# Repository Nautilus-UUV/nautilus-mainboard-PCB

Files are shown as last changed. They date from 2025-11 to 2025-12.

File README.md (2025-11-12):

# Nautilus Mainboard PCB
## Overview
This PCB houses an [STM32H7B0RBT6](https://www.st.com/resource/en/datasheet/stm32h7b0ab.pdf) together with a [CM4](https://pip-assets.raspberrypi.com/categories/634-raspberry-pi-compute-module-4/documents/RP-008168-DS-1-cm4-datasheet.pdf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). The STM32 is primarily used for communication over CanOpen with all the other PCBs while the CM4 is intended to run higher level calculations and then being shut off again. The CM4 is connected to an SSD. The CM4 and STM are connected over Uart (RX, TX) closely for communication and there is an integrated option for the STM to power off and on the CM4. (Currently the CM4's RUN_PG is connected to the STM32's pin number 10.) The STM has a crystal while the CM4 currently does not have one since it was not requested.

Additionally the mainboard provides two IMUs ([BMI088](https://www.bosch-sensortec.com/media/boschsensortec/downloads/datasheets/bst-bmi088-ds001.pdf)) that can be accessed over I^2C by the STM32. Those components house accelerometers and gyroscopes for orientation and movement detection and listen to the following addresses:
- Accelerometer: 0x18, 0x19
- Gyroscope: 0x68, 0x69

The Power supply is primarily provided by the UUV's battery lines (5V, 3.3V and GND) but the board also accepts USB-C 2.0 for both data and power inputs (only powering the CM4 and nothing else) or the 3.3V Power supply over the STM programmer pins. (only powers the STM32) The power logic is achieved using three [TPS2121RUXT](https://www.ti.com/lit/ds/symlink/tps2120.pdf?ts=1761678178328) (one for 5V, one for 3.3V and one for the GPIO reference of both microcontrollers.)

> [!CAUTION]
> The Power supply logic can be bypassed completely by soldering on 0 Ohm resistors on the designated spots for both 5V and 3.3V, but this still needs to be worked on.

### WIP

Differential pairs have been routed and matched in length but the trace widths still need to be recalculated and adjusted.

The whole board works on 2 layers with an additional ground layer in mind (until now 1 free layer)

If someone wants to write a better README, feel free to do so, I'd appreciate it.

This PCB has not yet been reviewed or tested.

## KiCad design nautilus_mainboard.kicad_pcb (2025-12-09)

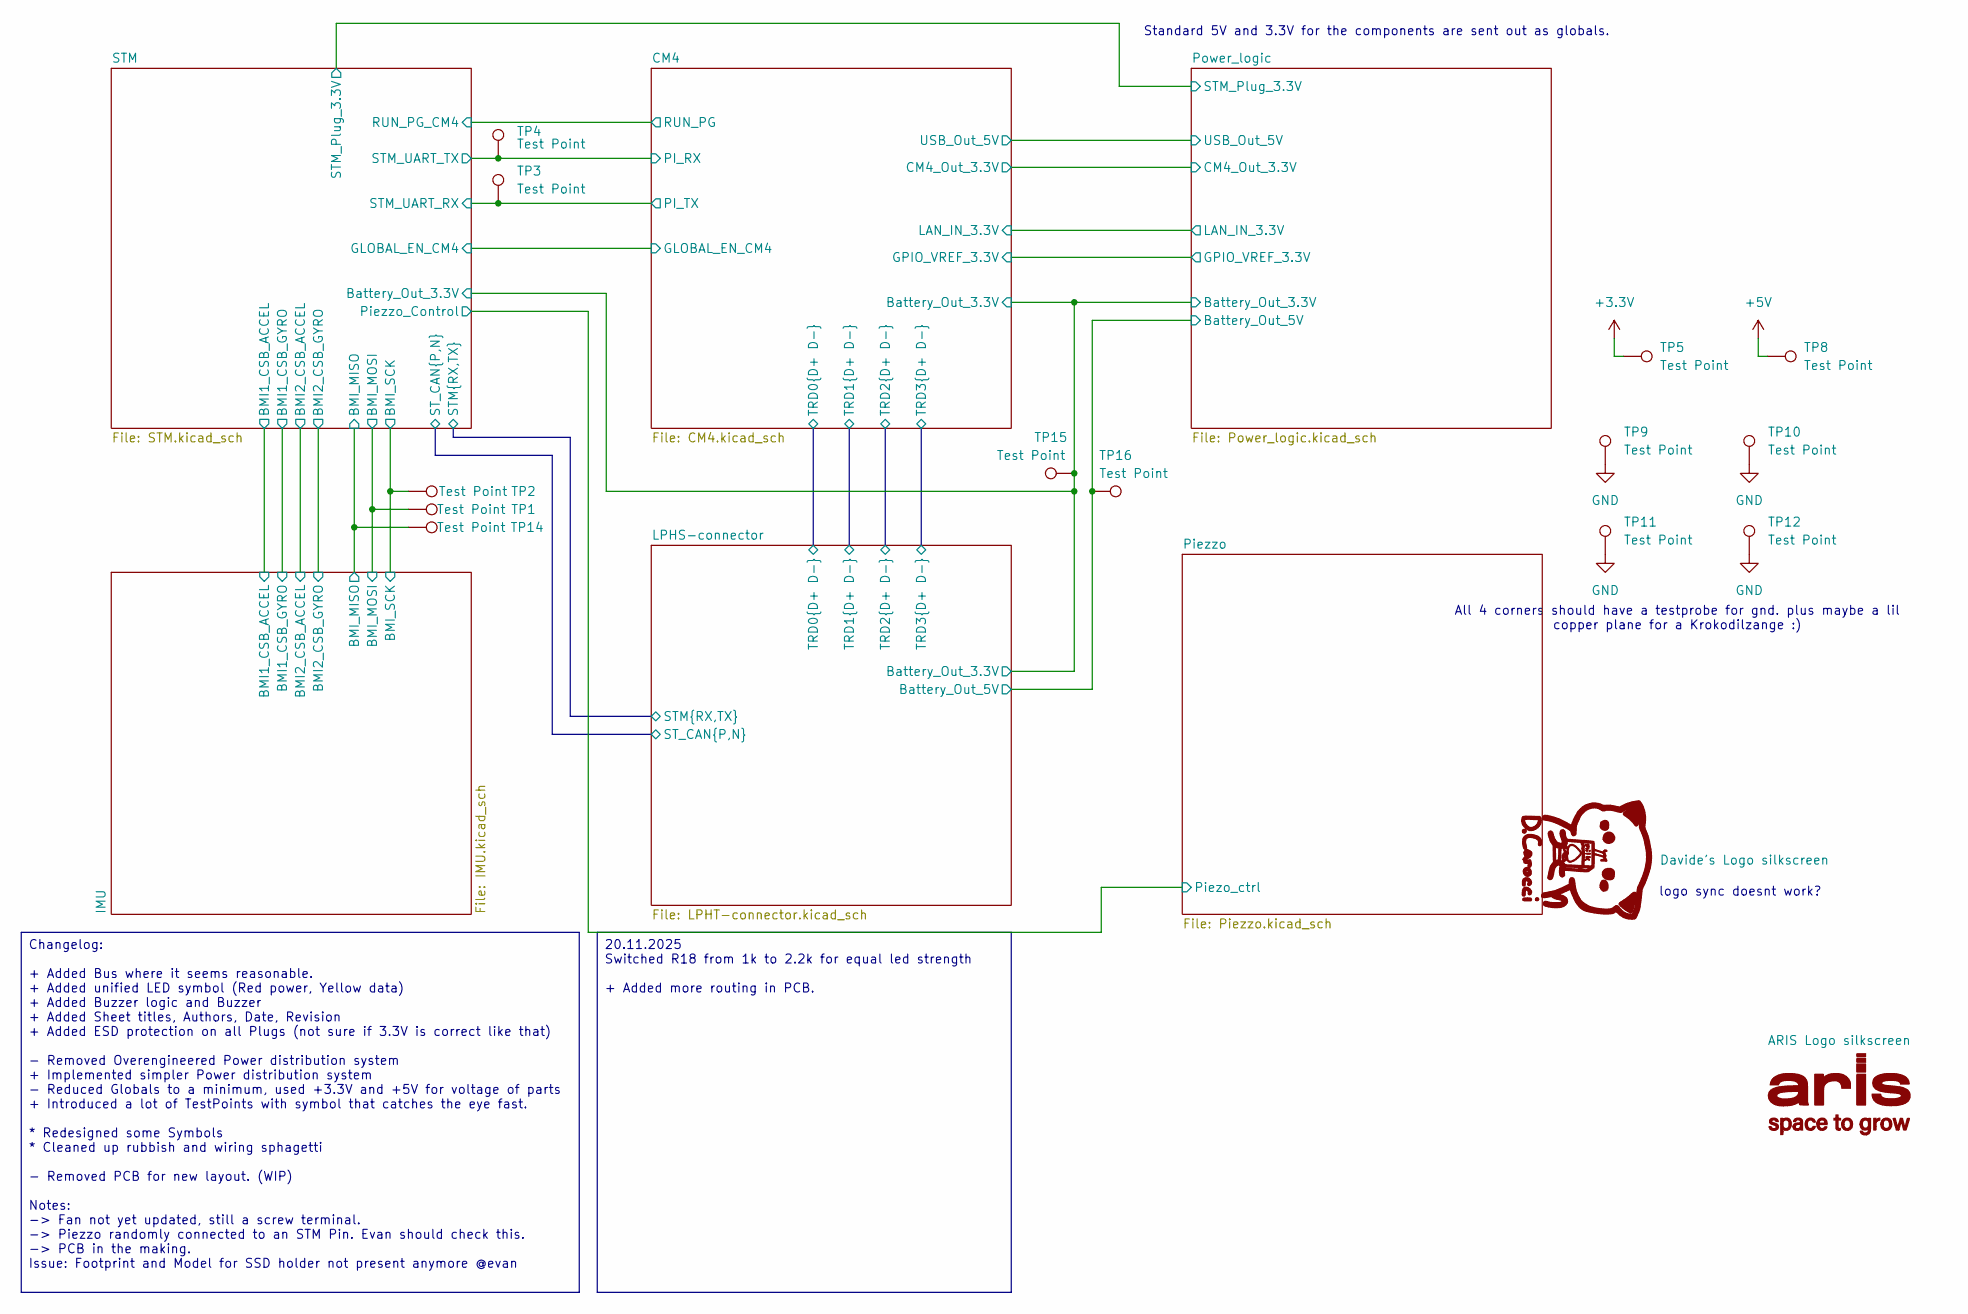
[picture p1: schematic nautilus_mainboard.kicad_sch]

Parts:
TP1, TP2, TP3, TP4, TP5, TP8, TP9, TP10, TP11, TP12, TP14, TP15, TP16: Test Point; TestPoint_Pad_D1.5mm

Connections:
+3.3V: TP5.1; also elsewhere on the board
+5V: TP8.1; also elsewhere on the board
/CM4/Battery_Out_3.3V: TP15.1; also elsewhere on the board
/IMU/BMI_MISO: TP14.1; also elsewhere on the board
/IMU/BMI_MOSI: TP1.1; also elsewhere on the board
/IMU/BMI_SCK: TP2.1; also elsewhere on the board
/LPHS-connector/Battery_Out_5V: TP16.1; also elsewhere on the board
/STM/PinoutSTM/USART2_RX: TP3.1; also elsewhere on the board
/STM/PinoutSTM/USART2_TX: TP4.1; also elsewhere on the board
GND: TP9.1, TP10.1, TP11.1, TP12.1; also elsewhere on the board

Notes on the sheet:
Standard 5V and 3.3V for the components are sent out as globals.
All 4 corners should have a testprobe for gnd. plus maybe a lil copper plane for a Krokodilzange :)
logo sync doesnt work?
20.11.2025 Switched R18 from 1k to 2.2k for equal led strength + Added more routing in PCB.
Changelog: + Added Bus where it seems reasonable. + Added unified LED symbol (Red power, Yellow data) + Added Buzzer logic and Buzzer + Added Sheet titles, Authors, Date, Revision + Added ESD protection on all Plugs (not sure if 3.3V is correct like that) - Removed Overengineered Power distribution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

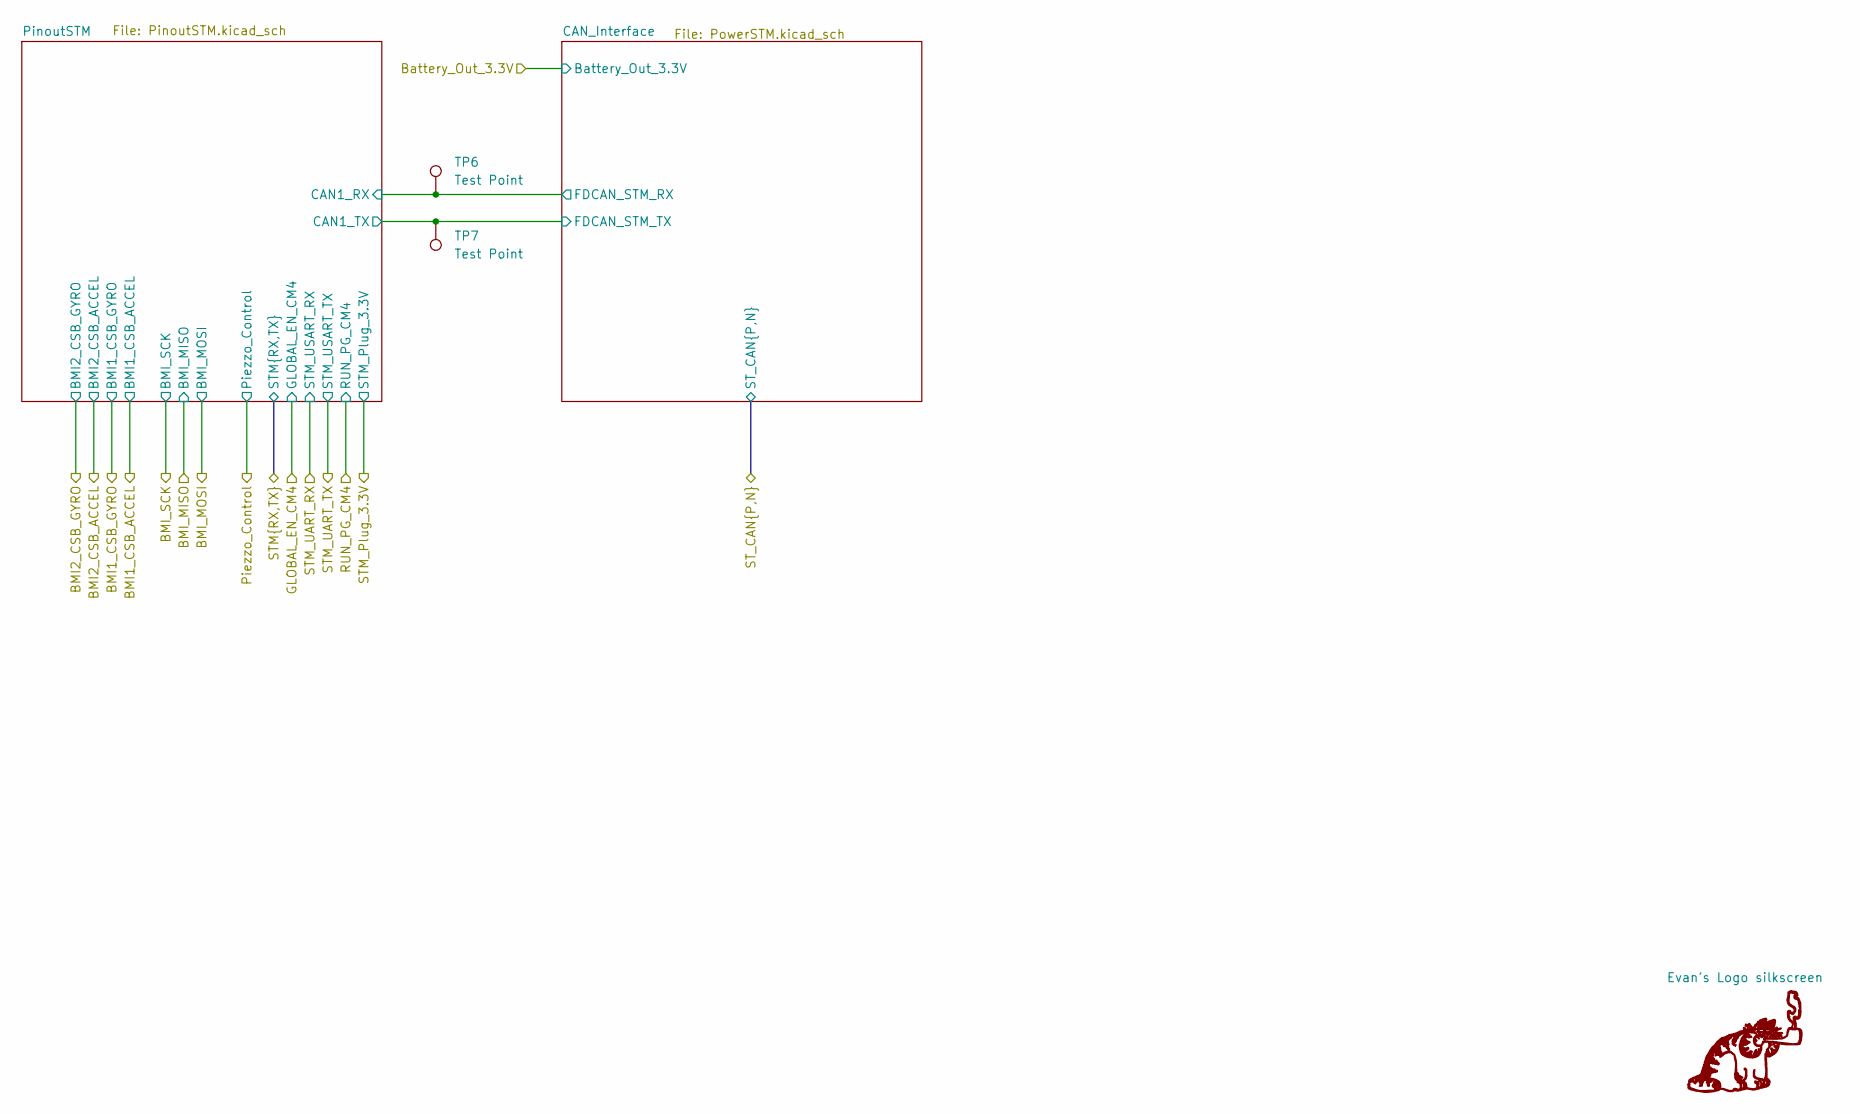
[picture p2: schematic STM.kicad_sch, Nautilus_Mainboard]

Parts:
TP6, TP7: Test Point; TestPoint_Pad_D1.5mm

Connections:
/STM/PinoutSTM/CAN1_RX: TP6.1; also elsewhere on the board
/STM/PinoutSTM/CAN1_TX: TP7.1; also elsewhere on the board

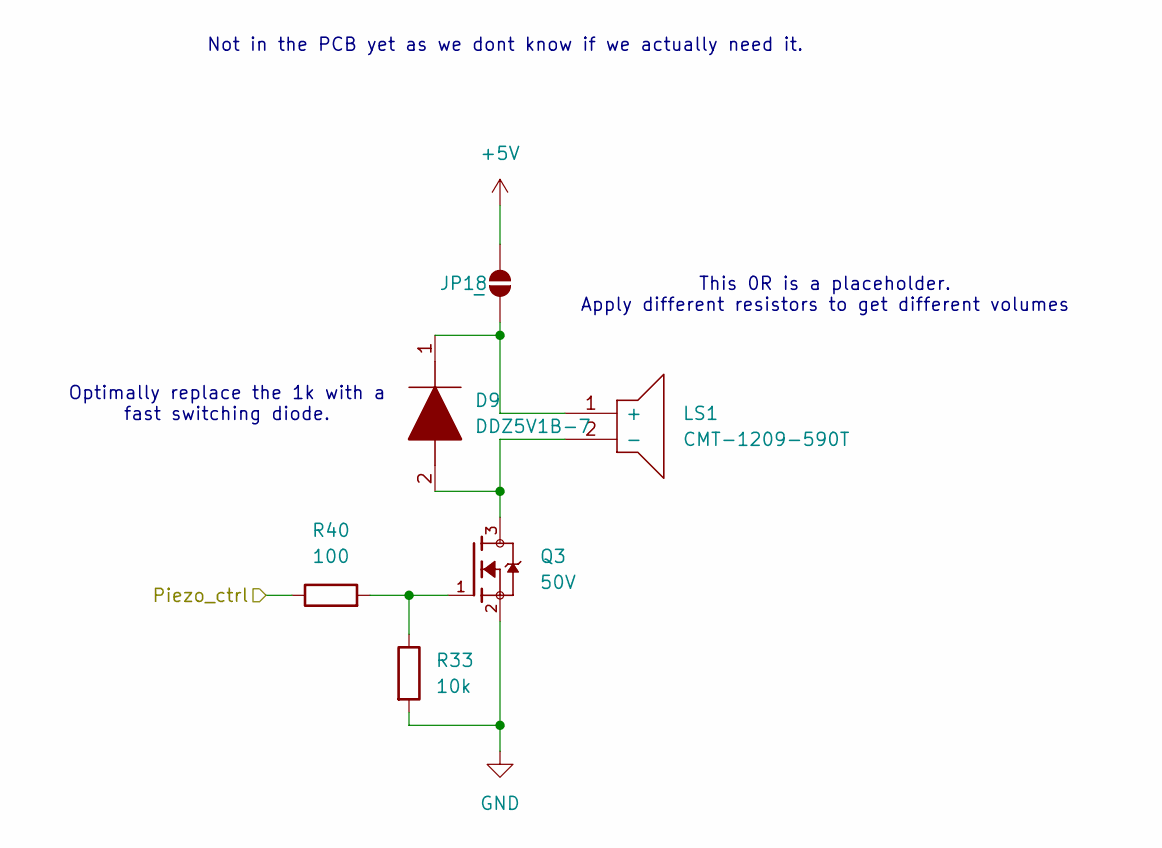
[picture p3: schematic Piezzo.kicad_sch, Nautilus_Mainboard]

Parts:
D9: DDZ5V1B-7; SOD3716X145N; Mouser Part Number 621-DDZ5V1B-7
JP18: -; SolderJumper-2_P1.3mm_Open_RoundedPad1.0x1.5mm
LS1: Piezo Buzzers & Audio Indicators 12mmx9mm deep Ma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; CMT1209590T; Mouser Part Number 179-CMT-1209-590T
Q3: 50V; onsemi_Mosfet_BSS138; PARTREV 30 Jan 2018
R33: 10k; R_0603_1608Metric; Tolerance 1 %; MPN 560112116005; LCSC CXXXXX
R40: 100; R_0402_1005Metric; Tolerance 1%; MPN ERJ-2RKF1000X; LCSC C413063

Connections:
+5V: JP18.2 (B); also elsewhere on the board
/Piezzo/Piezo_ctrl: R40.1; also elsewhere on the board
GND: Q3.2, R33.2; also elsewhere on the board
unnamed: D9.1, JP18.1 (A), LS1.1 (+)
unnamed: D9.2, LS1.2 (-), Q3.3
unnamed: Q3.1, R33.1, R40.2

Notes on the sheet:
Optimally replace the 1k with a fast switching diode.
This 0R is a placeholder. Apply different resistors to get different volumes
Not in the PCB yet as we dont know if we actually need it.

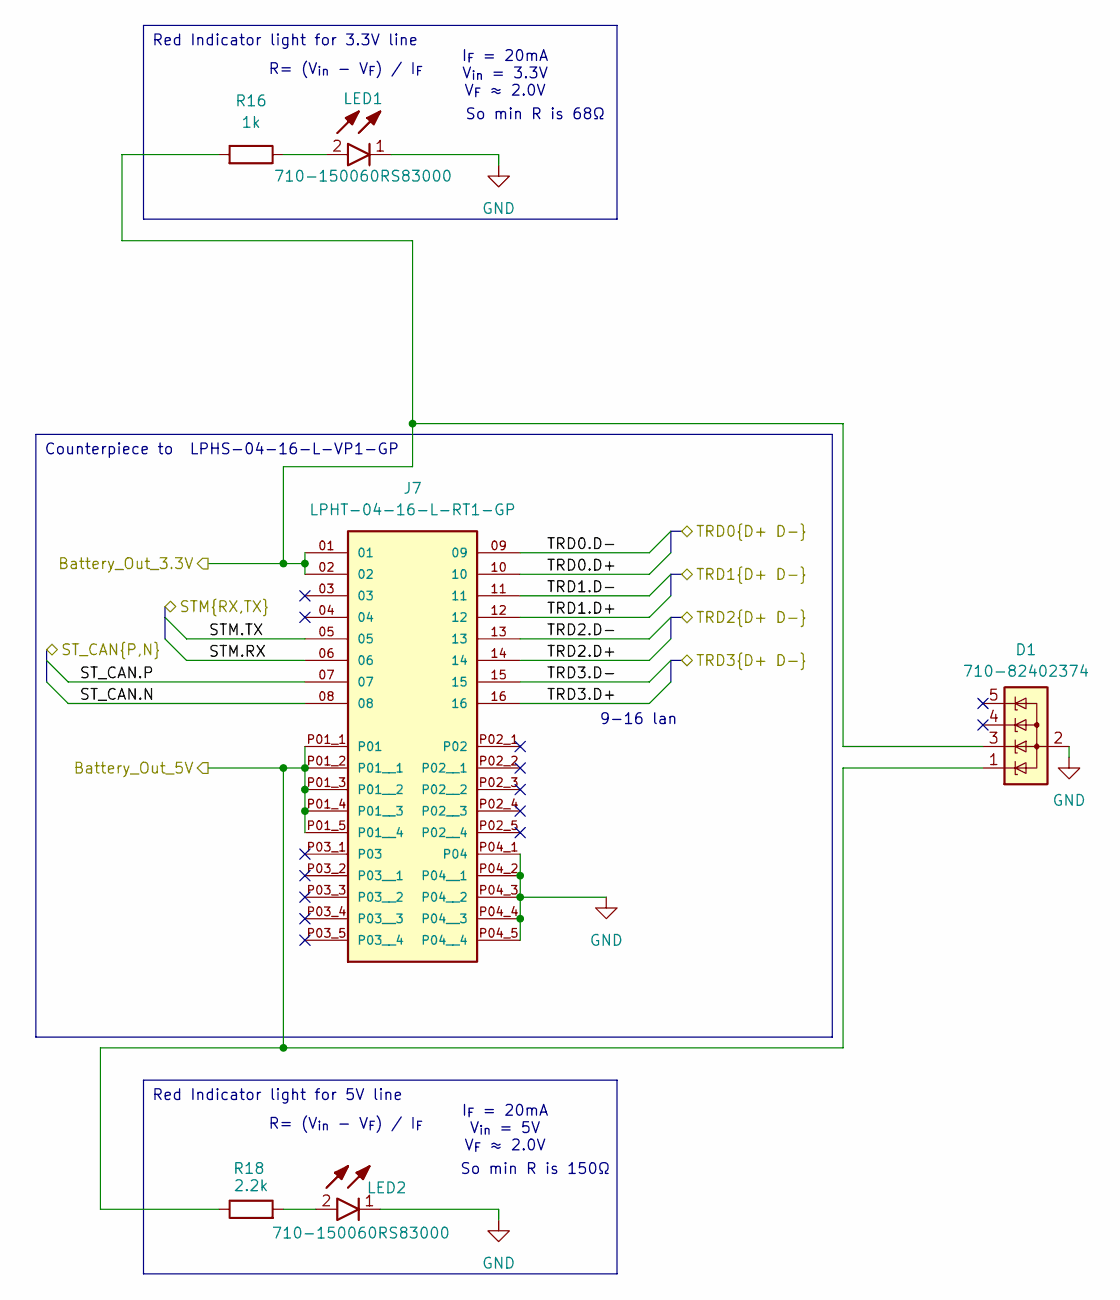
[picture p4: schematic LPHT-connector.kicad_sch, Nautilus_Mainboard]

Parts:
D1: 710-82402374; SOT-23-5; MPN 710-82402374
J7: LPHT-04-16-L-RT1-GP; SAMTEC_LPHT-04-16-X-RT1-GP; PARTREV C; LCSC CXXXXX
LED1, LED2: 710-150060RS83000; Wuerth_LED_150060RS83000; Manufacturer_Part_Number 150060RS83000
R16: 1k; R_0603_1608Metric; Tolerance 1 %; MPN 560112116014; LCSC CXXXXX
R18: 2.2k; R_0603_1608Metric; Tolerance 1 %; MPN 560112116098; LCSC CXXXXX

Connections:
/CM4/Battery_Out_3.3V: D1.3 (K), J7.01, J7.02, R16.2; also elsewhere on the board
/CM4/TRD0.D+: J7.10; also elsewhere on the board
/CM4/TRD0.D-: J7.09; also elsewhere on the board
/CM4/TRD1.D+: J7.12; also elsewhere on the board
/CM4/TRD1.D-: J7.11; also elsewhere on the board
/CM4/TRD2.D+: J7.14; also elsewhere on the board
/CM4/TRD2.D-: J7.13; also elsewhere on the board
/CM4/TRD3.D+: J7.16; also elsewhere on the board
/CM4/TRD3.D-: J7.15; also elsewhere on the board
/LPHS-connector/Battery_Out_5V: D1.1 (K), J7.P01_1 (P01), J7.P01_2 (P01__1), J7.P01_3 (P01__2), J7.P01_4 (P01__3), J7.P01_5 (P01__4), R18.1; also elsewhere on the board
/LPHS-connector/STM.RX: J7.06; also elsewhere on the board
/LPHS-connector/STM.TX: J7.05; also elsewhere on the board
/LPHS-connector/ST_CAN.N: J7.08; also elsewhere on the board
/LPHS-connector/ST_CAN.P: J7.07; also elsewhere on the board
GND: D1.2 (A), J7.P04_1 (P04), J7.P04_2 (P04__1), J7.P04_3 (P04__2), J7.P04_4 (P04__3), J7.P04_5 (P04__4), LED1.1 (K), LED2.1 (K); also elsewhere on the board
unnamed: LED1.2 (A), R16.1
unnamed: LED2.2 (A), R18.2

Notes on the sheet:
9-16 lan
I_{F} = 20mA V_{in} = 5V V_{F} ≈ 2.0V
R= (V_{in} - V_{F}) / I_{F}
So min R is 150Ω
So min R is 68Ω
I_{F} = 20mA V_{in} = 3.3V V_{F} ≈ 2.0V
Counterpiece to LPHS-04-16-L-VP1-GP
Red Indicator light for 3.3V line
Red Indicator light for 5V line

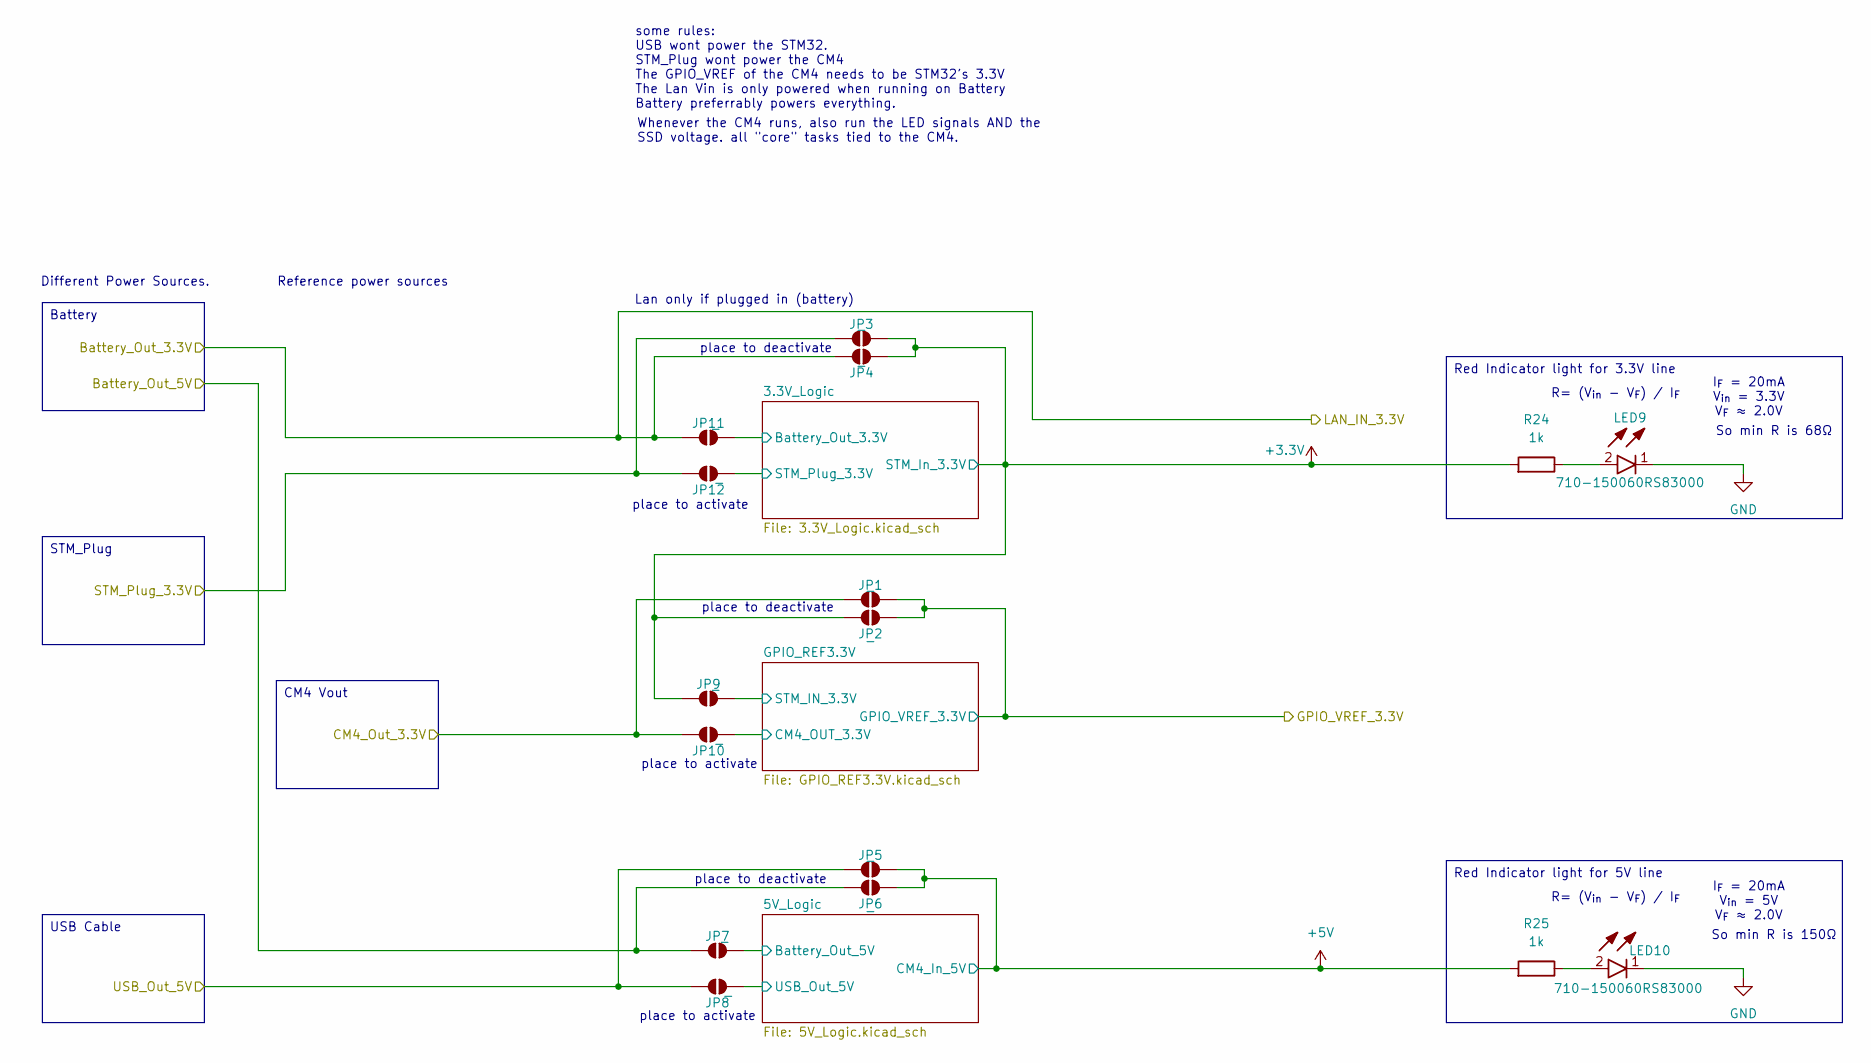
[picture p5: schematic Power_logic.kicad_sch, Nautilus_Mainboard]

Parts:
JP1, JP2, JP3, JP4, JP5, JP6, JP7, JP8, JP9, JP10, JP11, JP12: -; SolderJumper-2_P1.3mm_Open_RoundedPad1.0x1.5mm
LED9, LED10: 710-150060RS83000; Wuerth_LED_150060RS83000; Manufacturer_Part_Number 150060RS83000
R24, R25: 1k; R_0603_1608Metric; Tolerance 1 %; MPN 560112116014; LCSC CXXXXX

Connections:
+3.3V: JP2.1 (A), JP3.2 (B), JP4.2 (B), JP9.1 (A), R24.2; also elsewhere on the board
+5V: JP5.2 (B), JP6.2 (B), R25.2; also elsewhere on the board
/CM4/Battery_Out_3.3V: JP4.1 (A), JP11.1 (A); also elsewhere on the board
/CM4/CM4_Out_3.3V: JP1.1 (A), JP10.1 (A); also elsewhere on the board
/CM4/GPIO_VREF_3.3V: JP1.2 (B), JP2.2 (B); also elsewhere on the board
/CM4/USB_Out_5V: JP5.1 (A), JP8.1 (A); also elsewhere on the board
/LPHS-connector/Battery_Out_5V: JP6.1 (A), JP7.1 (A); also elsewhere on the board
/Power_logic/3.3V_Logic/Battery_Out_3.3V: JP11.2 (B); also elsewhere on the board
/Power_logic/3.3V_Logic/STM_Plug_3.3V: JP12.2 (B); also elsewhere on the board
/Power_logic/5V_Logic/Battery_Out_5V: JP7.2 (B); also elsewhere on the board
/Power_logic/5V_Logic/USB_Out_5V: JP8.2 (B); also elsewhere on the board
/Power_logic/GPIO_REF3.3V/CM4_OUT_3.3V: JP10.2 (B); also elsewhere on the board
/Power_logic/GPIO_REF3.3V/STM_IN_3.3V: JP9.2 (B); also elsewhere on the board
/Power_logic/STM_Plug_3.3V: JP3.1 (A), JP12.1 (A); also elsewhere on the board
GND: LED9.1 (K), LED10.1 (K); also elsewhere on the board
unnamed: LED9.2 (A), R24.1
unnamed: LED10.2 (A), R25.1

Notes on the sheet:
place to activate
Whenever the CM4 runs, also run the LED signals AND the SSD voltage. all "core" tasks tied to the CM4.
I_{F} = 20mA V_{in} = 3.3V V_{F} ≈ 2.0V
Different Power Sources.
R= (V_{in} - V_{F}) / I_{F}
some rules: USB wont power the STM32. STM_Plug wont power the CM4 The GPIO_VREF of the CM4 needs to be STM32's 3.3V The Lan Vin is only powered when running on Battery Battery preferrably powers everything.
place to deactivate
So min R is 150Ω
Lan only if plugged in (battery)
I_{F} = 20mA V_{in} = 5V V_{F} ≈ 2.0V
Reference power sources
So min R is 68Ω
CM4 Vout
Red Indicator light for 5V line
USB Cable
Battery
STM_Plug
Red Indicator light for 3.3V line

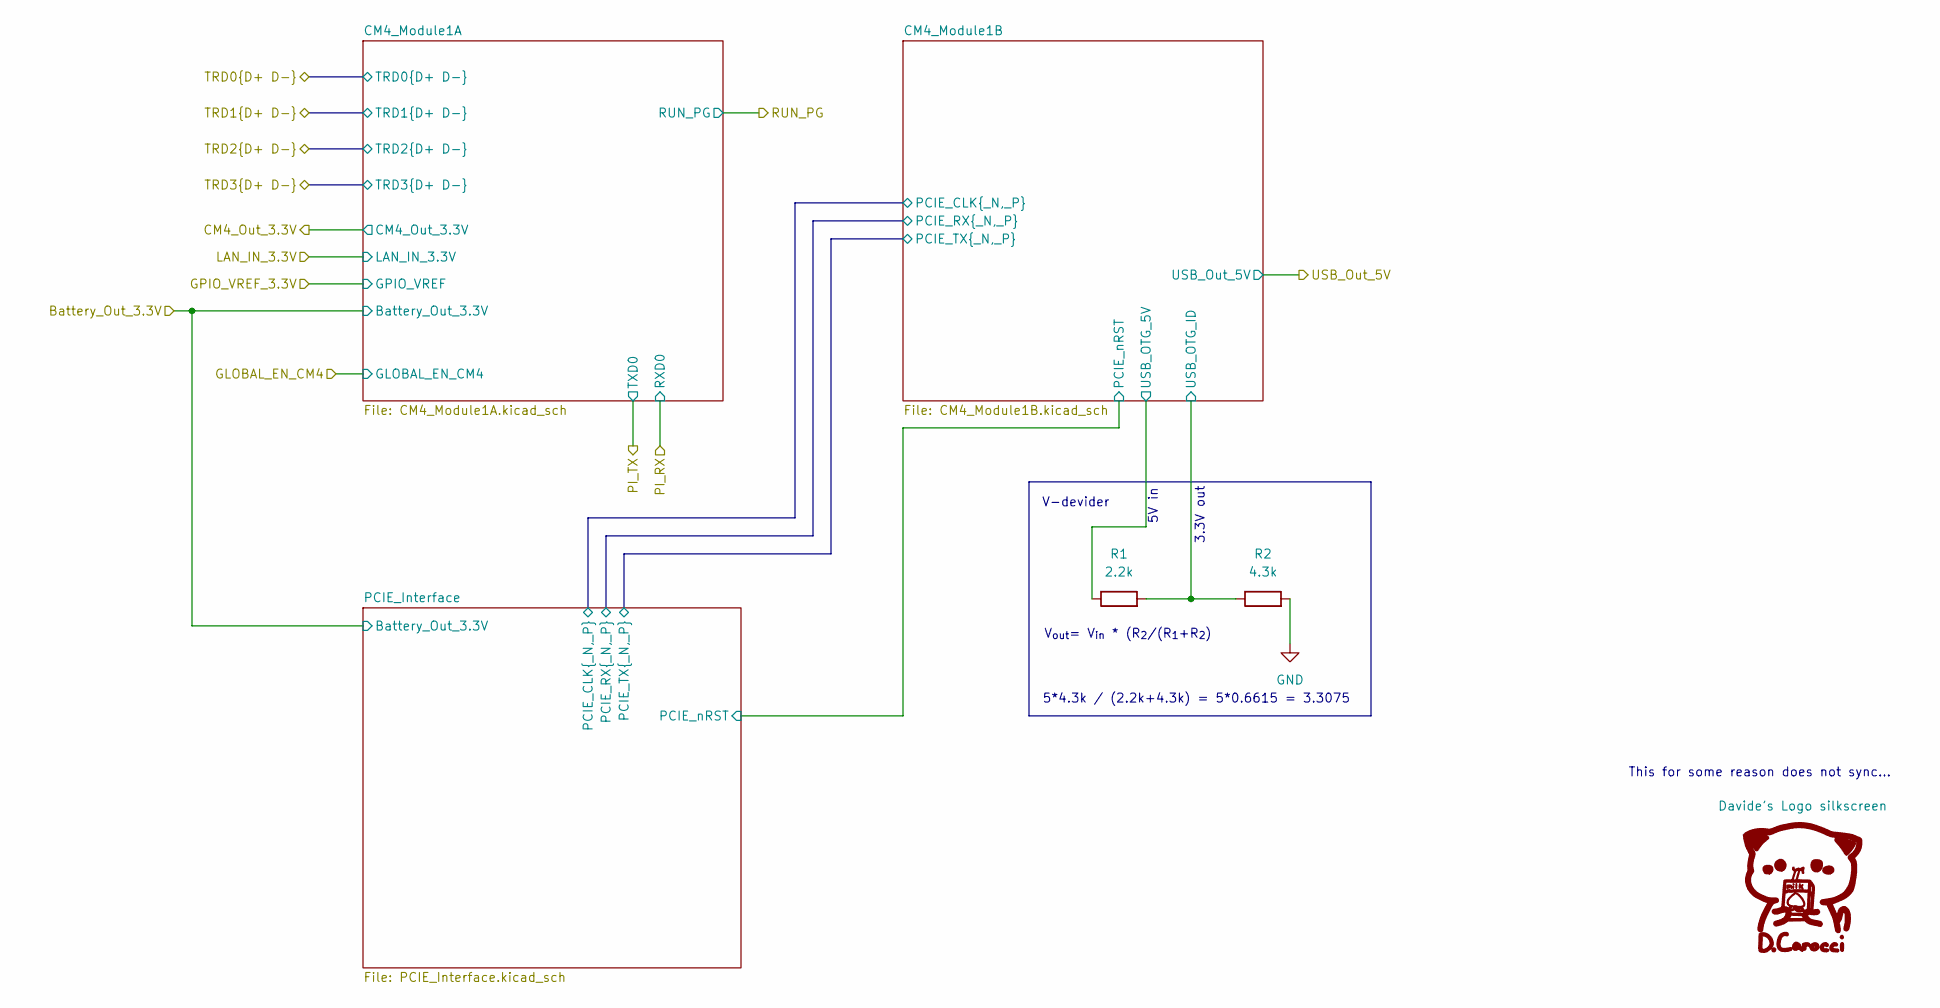
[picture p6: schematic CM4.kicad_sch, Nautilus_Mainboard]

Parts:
R1: 2.2k; R_0603_1608Metric; Tolerance 1 %; MPN 560112116098; LCSC CXXXXX
R2: 4.3k; R_0603_1608Metric; Tolerance 1 %; MPN 560112116141; LCSC CXXXXX

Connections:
/CM4/CM4_Module1B/USB_OTG_ID: R1.2, R2.1; also elsewhere on the board
/CM4/USB_Out_5V: R1.1; also elsewhere on the board
GND: R2.2; also elsewhere on the board

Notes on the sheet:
This for some reason does not sync...
5V in
V-devider
5*4.3k / (2.2k+4.3k) = 5*0.6615 = 3.3075
3.3V out
V_{out}= V_{in} * (R_{2}/(R_{1}+R_{2})

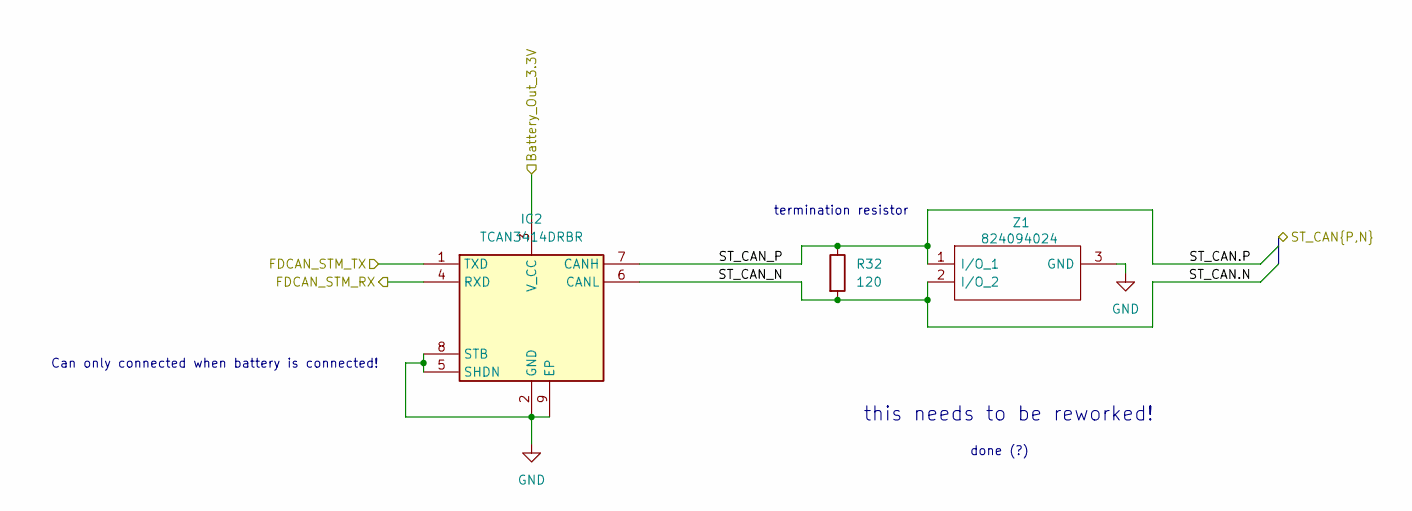
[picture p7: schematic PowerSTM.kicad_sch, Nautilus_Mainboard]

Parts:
IC2: TCAN3414DRBR; Mouser Part Number 595-TCAN3414DRBR
R32: 120; R_0603_1608Metric; Tolerance 1%; MPN 560112116119; LCSC CXXXXX
Z1: 824094024; SOT95P240X104-3N; Mouser Part Number 710-824094024

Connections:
/CM4/Battery_Out_3.3V: IC2.3 (V_CC); also elsewhere on the board
/LPHS-connector/ST_CAN.N: IC2.6 (CANL), R32.2, Z1.2 (I/O_2); also elsewhere on the board
/LPHS-connector/ST_CAN.P: IC2.7 (CANH), R32.1, Z1.1 (I/O_1); also elsewhere on the board
/STM/PinoutSTM/CAN1_RX: IC2.4 (RXD); also elsewhere on the board
/STM/PinoutSTM/CAN1_TX: IC2.1 (TXD); also elsewhere on the board
GND: IC2.2 (GND), IC2.5 (SHDN), IC2.8 (STB), IC2.9 (EP), Z1.3 (GND); also elsewhere on the board

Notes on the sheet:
Can only connected when battery is connected!
done (?)
termination resistor
this needs to be reworked!

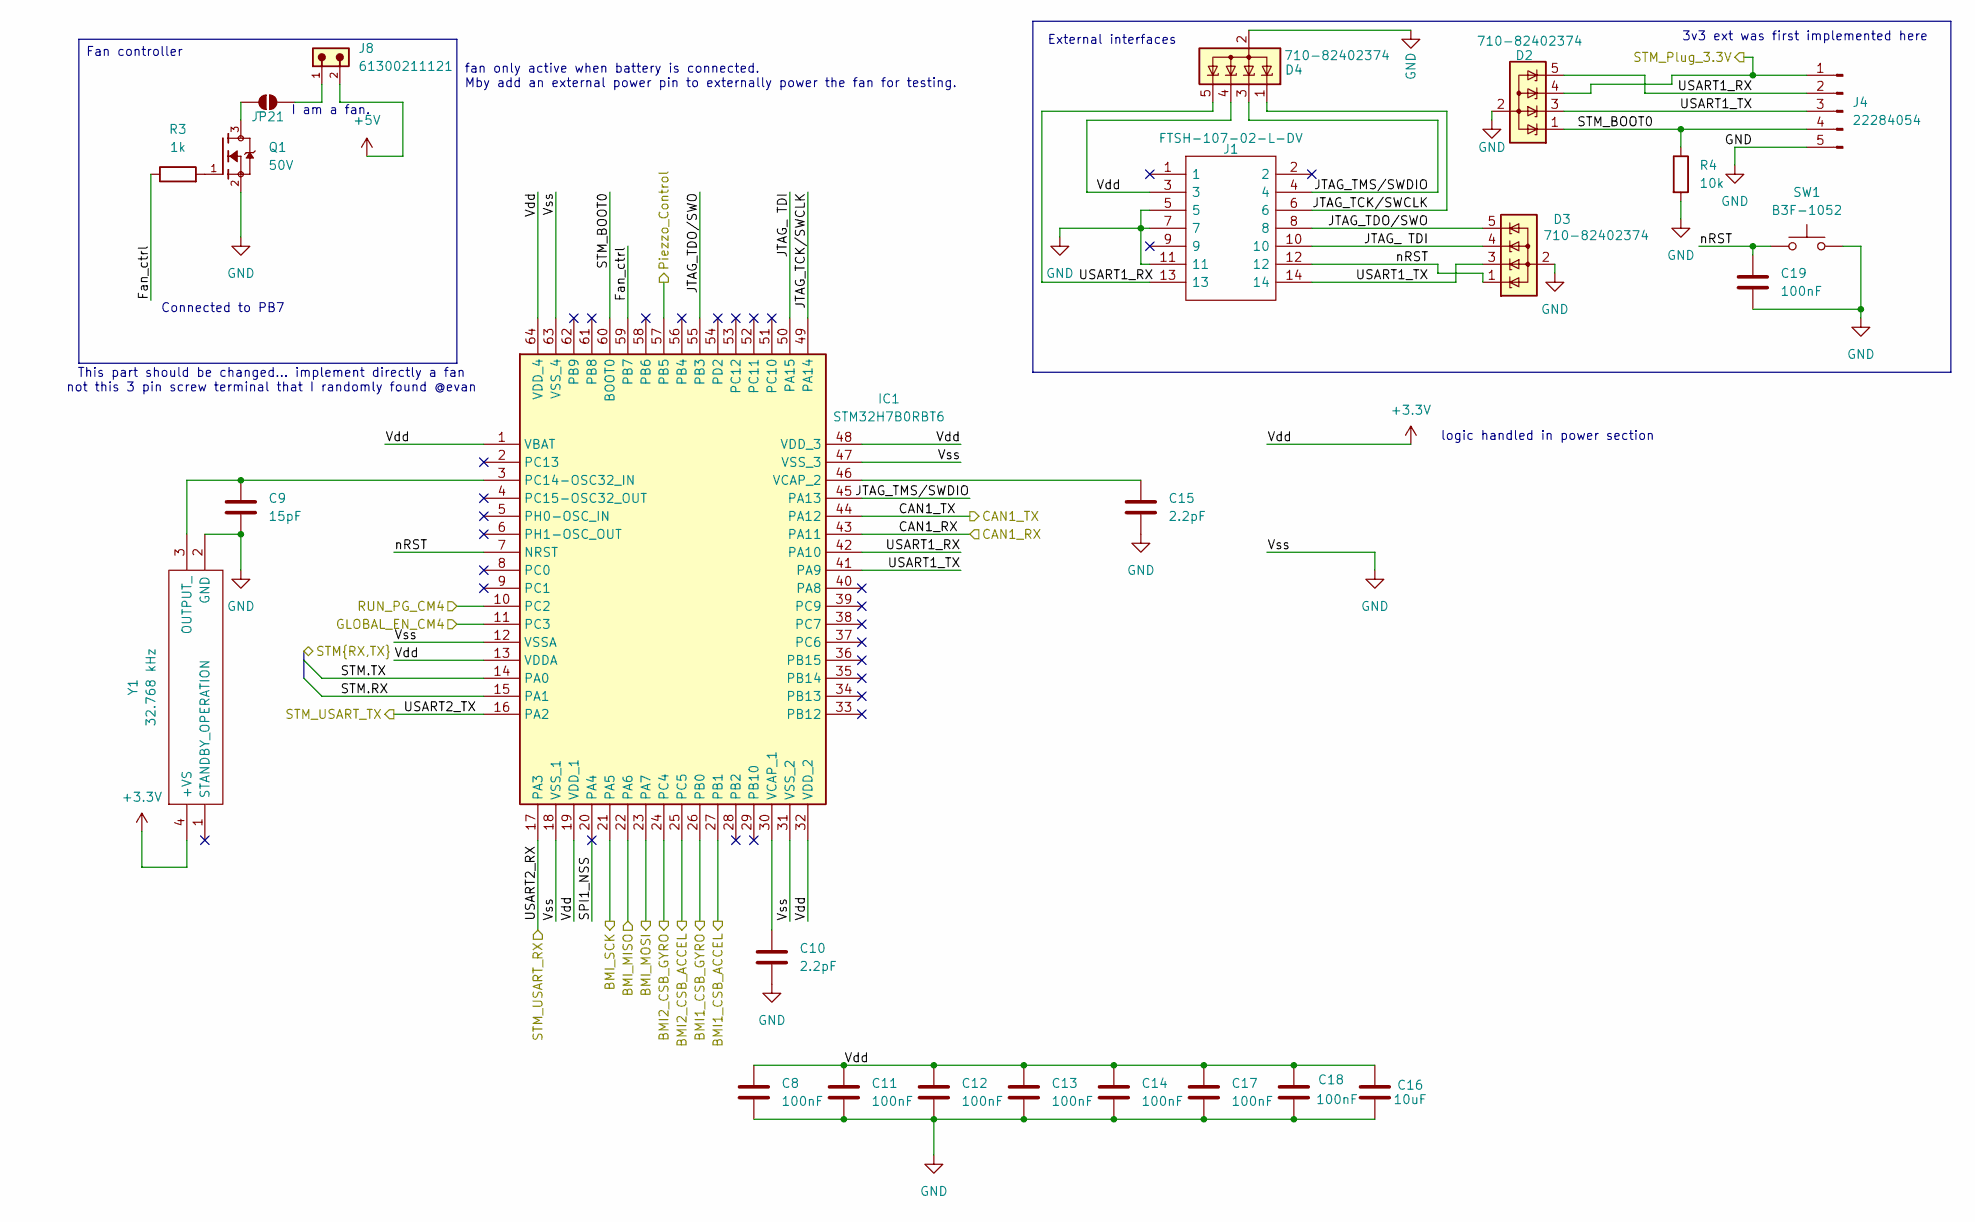
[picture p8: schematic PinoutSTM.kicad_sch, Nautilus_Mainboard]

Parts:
C8, C11, C12, C13, C14, C17, C18, C19: 100nF; C_0603_1608Metric; Voltage 50V; Tolerance 10%; MPN 885012206095; LCSC CXXXXX
C9: 15pF; C_0603_1608Metric; Voltage 50V; Tolerance 5%; MPN 885012006052; LCSC CXXXXX
C10, C15: 2.2pF; C_0603_1608Metric; Voltage 50V; Tolerance ±0.5pF; MPN 885012006047; LCSC CXXXXX
C16: 10uF; C_1210_3225Metric; Voltage 100V; Tolerance 10%; MPN GRM32EC72A106KE05; LCSC C5444485
D2, D3, D4: 710-82402374; SOT-23-5; MPN 710-82402374
IC1: STM32H7B0RBT6; LQFP-64_10x10mm_P0.5mm; Voltage 1.62V - 3.6V; Mouser Part Number 511-STM32H7B0RBT6
J1: FTSH-107-02-L-DV; FTSH-107-XX-YYY-DV; Mouser Part Number 200-FTSH10702LDV
J4: Header male 1x05; PinHeader_1x05_P2.54mm_Vertical; MPN 22284054; LCSC C7501263
J8: 61300211121; Wurth_Con_61300211121; MPN 61300211121
JP21: -; SolderJumper-2_P1.3mm_Open_RoundedPad1.0x1.5mm
Q1: 50V; onsemi_Mosfet_BSS138; PARTREV 30 Jan 2018
R3: 1k; R_0603_1608Metric; Tolerance 1 %; MPN 560112116014; LCSC CXXXXX
R4: 10k; R_0603_1608Metric; Tolerance 1 %; MPN 560112116005; LCSC CXXXXX
SW1: Button Switch SPST-No; SW_PUSH_6mm; MPN B3F-1052; LCSC C87037
Y1: 32.768 kHz; 830205028309; Mouser Part Number 710-830205028309

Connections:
+3.3V: C8.1, C11.1, C12.1, C13.1, C14.1, C16.1, C17.1, C18.1, D4.4 (K), IC1.1 (VBAT), IC1.13 (VDDA), IC1.19 (VDD_1), IC1.32 (VDD_2), IC1.48 (VDD_3), IC1.64 (VDD_4), J1.3, Y1.4 (+VS); also elsewhere on the board
+5V: J8.2; also elsewhere on the board
/CM4/GLOBAL_EN_CM4: IC1.11 (PC3); also elsewhere on the board
/CM4/RUN_PG: IC1.10 (PC2); also elsewhere on the board
/IMU/BMI1_CSB_ACCEL: IC1.27 (PB1); also elsewhere on the board
/IMU/BMI1_CSB_GYRO: IC1.26 (PB0); also elsewhere on the board
/IMU/BMI2_CSB_ACCEL: IC1.25 (PC5); also elsewhere on the board
/IMU/BMI2_CSB_GYRO: IC1.24 (PC4); also elsewhere on the board
/IMU/BMI_MISO: IC1.22 (PA6); also elsewhere on the board
/IMU/BMI_MOSI: IC1.23 (PA7); also elsewhere on the board
/IMU/BMI_SCK: IC1.21 (PA5); also elsewhere on the board
/LPHS-connector/STM.RX: IC1.15 (PA1); also elsewhere on the board
/LPHS-connector/STM.TX: IC1.14 (PA0); also elsewhere on the board
/Piezzo/Piezo_ctrl: IC1.57 (PB5); also elsewhere on the board
/Power_logic/STM_Plug_3.3V: D2.4 (K), J4.1; also elsewhere on the board
/STM/PinoutSTM/CAN1_RX: IC1.43 (PA11); also elsewhere on the board
/STM/PinoutSTM/CAN1_TX: IC1.44 (PA12); also elsewhere on the board
/STM/PinoutSTM/Fan_ctrl: IC1.59 (PB7), R3.1
/STM/PinoutSTM/JTAG_ TDI: D3.4 (K), IC1.50 (PA15), J1.10
/STM/PinoutSTM/JTAG_TCK/SWCLK: D4.1 (K), IC1.49 (PA14), J1.6
/STM/PinoutSTM/JTAG_TDO/SWO: D3.5 (K), IC1.55 (PB3), J1.8
/STM/PinoutSTM/JTAG_TMS/SWDIO: D4.3 (K), IC1.45 (PA13), J1.4
/STM/PinoutSTM/SPI1_NSS: IC1.20 (PA4)
/STM/PinoutSTM/STM_BOOT0: D2.1 (K), IC1.60 (BOOT0), J4.4, R4.1
/STM/PinoutSTM/USART1_RX: D2.5 (K), D4.5 (K), IC1.42 (PA10), J1.13, J4.2
/STM/PinoutSTM/USART1_TX: D2.3 (K), D3.3 (K), IC1.41 (PA9), J1.14, J4.3
/STM/PinoutSTM/USART2_RX: IC1.17 (PA3); also elsewhere on the board
/STM/PinoutSTM/USART2_TX: IC1.16 (PA2); also elsewhere on the board
/STM/PinoutSTM/nRST: C19.1, D3.1 (K), IC1.7 (NRST), J1.12, SW1.1
GND: C8.2, C9.2, C10.2, C11.2, C12.2, C13.2, C14.2, C15.2, C16.2, C17.2, C18.2, C19.2, D2.2 (A), D3.2 (A), D4.2 (A), IC1.12 (VSSA), IC1.18 (VSS_1), IC1.31 (VSS_2), IC1.47 (VSS_3), IC1.63 (VSS_4), J1.5, J1.7, J1.11, J4.5, Q1.2, R4.2, SW1.2, Y1.2 (GND); also elsewhere on the board
unnamed: C9.1, IC1.3 (PC14-OSC32_IN), Y1.3 (OUTPUT_)
unnamed: C10.1, IC1.30 (VCAP_1)
unnamed: C15.1, IC1.46 (VCAP_2)
unnamed: J8.1, JP21.1 (A)
unnamed: JP21.2 (B), Q1.3
unnamed: Q1.1, R3.2

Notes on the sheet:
I am a fan.
Connected to PB7
fan only active when battery is connected. Mby add an external power pin to externally power the fan for testing.
logic handled in power section
External interfaces
3v3 ext was first implemented here
This part should be changed... implement directly a fan not this 3 pin screw terminal that I randomly found @evan
Fan controller

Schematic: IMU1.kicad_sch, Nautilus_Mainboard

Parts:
C28, C29: 100nF; C_0603_1608Metric; Voltage 50V; Tolerance 10%; MPN 885012206095; LCSC CXXXXX
JP19: -; SolderJumper-2_P1.3mm_Open_RoundedPad1.0x1.5mm
U2: 262-BMI088; Bosch_IMU_BMI088; MPN 262-BMI088

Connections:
+3.3V: JP19.2 (B); also elsewhere on the board
/IMU/BMI2_CSB_ACCEL: U2.14 (CSB1); also elsewhere on the board
/IMU/BMI2_CSB_GYRO: U2.5 (CSB2); also elsewhere on the board
/IMU/BMI_MISO: U2.10 (SDO2), U2.15 (SDO1); also elsewhere on the board
/IMU/BMI_MOSI: U2.9 (SDA/SDI); also elsewhere on the board
/IMU/BMI_SCK: U2.8 (SCL/SCK); also elsewhere on the board
/IMU/IMU2/VDD: C28.1, C29.1, JP19.1 (A), U2.3 (VDD), U2.11 (VDDIO)
GND: C28.2, C29.2, U2.2 (NC), U2.4 (GNDA), U2.6 (GNDIO), U2.7 (PS); also elsewhere on the board

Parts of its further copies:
C43, C44: 100nF; C_0603_1608Metric; Voltage 50V; Tolerance 10%; MPN 885012206095; LCSC CXXXXX
JP20: -; SolderJumper-2_P1.3mm_Open_RoundedPad1.0x1.5mm
U1: 262-BMI088; Bosch_IMU_BMI088; MPN 262-BMI088

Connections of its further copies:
+3.3V: JP20.2 (B); also elsewhere on the board
/IMU/BMI1_CSB_ACCEL: U1.14 (CSB1); also elsewhere on the board
/IMU/BMI1_CSB_GYRO: U1.5 (CSB2); also elsewhere on the board
/IMU/BMI_MISO: U1.10 (SDO2), U1.15 (SDO1); also elsewhere on the board
/IMU/BMI_MOSI: U1.9 (SDA/SDI); also elsewhere on the board
/IMU/BMI_SCK: U1.8 (SCL/SCK); also elsewhere on the board
/IMU/IMU1/VDD: C43.1, C44.1, JP20.1 (A), U1.3 (VDD), U1.11 (VDDIO)
GND: C43.2, C44.2, U1.2 (NC), U1.4 (GNDA), U1.6 (GNDIO), U1.7 (PS); also elsewhere on the board

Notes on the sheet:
Same voltage used for logic line
Those are for interrupts.
Kill power

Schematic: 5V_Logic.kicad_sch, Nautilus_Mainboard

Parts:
C35, C36: 10uF; C_1210_3225Metric; Voltage 100V; Tolerance 10%; MPN GRM32EC72A106KE05; LCSC C5444485
C37, C38, C40: 100nF; C_0603_1608Metric; Voltage 50V; Tolerance 10%; MPN 885012206095; LCSC CXXXXX
C41: 330nF; C_0603_1608Metric; Voltage 10V; Tolerance 20%; MPN 885012106007; LCSC CXXXXX
C53: 47uF; C_0805_2012Metric; Voltage 10V; Tolerance 20%; MPN GRM21BR61A476ME15; LCSC C124129
IC5: TPS2121RUXT; TI_Switchover_TPS2121RUXT; Mouser Part Number 595-TPS2121RUXT
R22: 22k; R_0603_1608Metric; Tolerance 1 %; MPN 560112116022; LCSC CXXXXX

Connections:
+5V: C40.1, C53.1, IC5.1 (OUT_1), IC5.8 (OUT_2); also elsewhere on the board
/Power_logic/5V_Logic/Battery_Out_5V: C35.1, C37.1, IC5.6 (PR1), IC5.7 (IN1); also elsewhere on the board
/Power_logic/5V_Logic/USB_Out_5V: C36.1, C38.1, IC5.2 (IN2); also elsewhere on the board
GND: C35.2, C36.2, C37.2, C38.2, C40.2, C41.1, C53.2, IC5.3 (CP2), IC5.4 (OV2), IC5.5 (OV1), IC5.12 (GND), R22.1; also elsewhere on the board
unnamed: IC5.10 (ILIM), R22.2
unnamed: C41.2, IC5.11 (SS)

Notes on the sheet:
for questions about wiring etc please consult the datasheet...
if the USB-only cold start "disconnects" we can try to bump SS to 470nF instead of 330nF.
100nF CLOSE
https://www.ti.com/lit/ds/symlink/tps2120.pdf?ts=1761678178328
PR1 > CP2 -> IN1 has prio

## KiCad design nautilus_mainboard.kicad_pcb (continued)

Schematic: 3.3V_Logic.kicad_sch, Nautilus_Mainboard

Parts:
C21, C22: 10uF; C_1210_3225Metric; Voltage 100V; Tolerance 10%; MPN GRM32EC72A106KE05; LCSC C5444485
C23, C24, C26: 100nF; C_0603_1608Metric; Voltage 50V; Tolerance 10%; MPN 885012206095; LCSC CXXXXX
C25: 330nF; C_0603_1608Metric; Voltage 10V; Tolerance 20%; MPN 885012106007; LCSC CXXXXX
C27: 47uF; C_0805_2012Metric; Voltage 10V; Tolerance 20%; MPN GRM21BR61A476ME15; LCSC C124129
IC6: TPS2121RUXT; TI_Switchover_TPS2121RUXT; Mouser Part Number 595-TPS2121RUXT
R17: 68k; R_0603_1608Metric; Tolerance 1 %; MPN 560112116064; LCSC CXXXXX

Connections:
+3.3V: C26.1, C27.1, IC6.1 (OUT_1), IC6.8 (OUT_2); also elsewhere on the board
/Power_logic/3.3V_Logic/Battery_Out_3.3V: C21.1, C23.1, IC6.6 (PR1), IC6.7 (IN1); also elsewhere on the board
/Power_logic/3.3V_Logic/STM_Plug_3.3V: C22.1, C24.1, IC6.2 (IN2); also elsewhere on the board
GND: C21.2, C22.2, C23.2, C24.2, C25.1, C26.2, C27.2, IC6.3 (CP2), IC6.4 (OV2), IC6.5 (OV1), IC6.12 (GND), R17.2; also elsewhere on the board
unnamed: IC6.10 (ILIM), R17.1
unnamed: C25.2, IC6.11 (SS)

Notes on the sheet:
if the USB-only cold start "disconnects" we can try to bump SS to 470nF instead of 330nF.
22 kΩ → ~4.55 A 39 kΩ → ~2.78 A 50 kΩ → ~2.25 A 56 kΩ → ~2.04 A 68 kΩ → ~1.72 A 100 kΩ → ~1.24 A
Pin 10: 68k leads to about 1.72A (should be enough for STM)
[R] = [kOhm] 65.2 / R^0.861
PR1 > CP2 -> IN1 has prio

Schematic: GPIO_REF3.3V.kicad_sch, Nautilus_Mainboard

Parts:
C39, C50, C51, C52: 100nF; C_0603_1608Metric; Voltage 50V; Tolerance 10%; MPN 885012206095; LCSC CXXXXX
C48, C49: 10uF; C_1210_3225Metric; Voltage 100V; Tolerance 10%; MPN GRM32EC72A106KE05; LCSC C5444485
C54: 47uF; C_0805_2012Metric; Voltage 10V; Tolerance 20%; MPN GRM21BR61A476ME15; LCSC C124129
IC3: TPS2121RUXT; TI_Switchover_TPS2121RUXT; Mouser Part Number 595-TPS2121RUXT
R14, R27: 100k; R_0603_1608Metric; Tolerance 1 %; MPN 560112116004; LCSC CXXXXX
TP13: Test Point; TestPoint_Pad_D1.5mm

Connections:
/CM4/GPIO_VREF_3.3V: C52.1, C54.1, IC3.1 (OUT_1), IC3.8 (OUT_2), R14.1, TP13.1; also elsewhere on the board
/Power_logic/GPIO_REF3.3V/CM4_OUT_3.3V: C49.1, C51.1, IC3.2 (IN2); also elsewhere on the board
/Power_logic/GPIO_REF3.3V/STM_IN_3.3V: C48.1, C50.1, IC3.6 (PR1), IC3.7 (IN1); also elsewhere on the board
GND: C39.1, C48.2, C49.2, C50.2, C51.2, C52.2, C54.2, IC3.3 (CP2), IC3.4 (OV2), IC3.5 (OV1), IC3.12 (GND), R14.2, R27.1; also elsewhere on the board
unnamed: IC3.10 (ILIM), R27.2
unnamed: C39.2, IC3.11 (SS)

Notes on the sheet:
Pin SS (11): 100nF soft start cap more than enoug as virtually no load at all at vref
PR1 > CP2 -> IN1 has prio
[R] = [kOhm] 65.2 / R^0.861
100kOhm pulldown so Vref is low if everything is off (not floating)
22 kΩ → ~4.55 A 39 kΩ → ~2.78 A 50 kΩ → ~2.25 A 56 kΩ → ~2.04 A 68 kΩ → ~1.72 A 100 kΩ → ~1.24 A
Pin 10: 100kOhm leads to about 1.24A (absolute overkill)

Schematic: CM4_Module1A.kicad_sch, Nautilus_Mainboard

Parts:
C1, C2, C3, C4, C5, C6: 100nF; C_0603_1608Metric; Voltage 50V; Tolerance 10%; MPN 885012206095; LCSC CXXXXX
C7, C42: 1uF; C_0603_1608Metric; Voltage 50V; Tolerance 10%; MPN 885012206126; LCSC CXXXXX
C47: 10uF; C_1210_3225Metric; Voltage 100V; Tolerance 10%; MPN GRM32EC72A106KE05; LCSC C5444485
Module1: DF40C-100DS-0.4V(51); Con-Raspberry-Pi-4-Compute-Module; Part Description 100 Position Connector Receptacle, Cent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; LCSC N/A
Q2: 50V; onsemi_Mosfet_BSS138; PARTREV 30 Jan 2018

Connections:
+5V: C1.1, C2.1, C3.1, C4.1, C5.1, C6.1, C7.1, C42.1, C47.1, Module1.77 (+5v_(Input)), Module1.79 (+5v_(Input)), Module1.81 (+5v_(Input)), Module1.83 (+5v_(Input)), Module1.85 (+5v_(Input)), Module1.87 (+5v_(Input)); also elsewhere on the board
/CM4/CM4_Module1A/CM4_LED1/nPWR_LED: Module1.95 (nPI_LED_PWR); also elsewhere on the board
/CM4/CM4_Module1A/CM4_LED2/PI_nLED_Activity: Module1.21 (PI_nLED_Activity); also elsewhere on the board
/CM4/CM4_Module1A/ETH_LED_G: Module1.15 (Ethernet_nLED3(3.3v)); also elsewhere on the board
/CM4/CM4_Module1A/ETH_LED_Y: Module1.17 (Ethernet_nLED2(3.3v)); also elsewhere on the board
/CM4/CM4_Module1A/GLOBAL_EN: Module1.99 (Global_EN), Q2.3
/CM4/CM4_Module1A/GPIO2: Module1.58 (GPIO2)
/CM4/CM4_Module1A/GPIO3: Module1.56 (GPIO3)
/CM4/CM4_Module1A/GPIO4: Module1.54 (GPIO4)
/CM4/CM4_Module1A/GPIO5: Module1.34 (GPIO5)
/CM4/CM4_Module1A/GPIO6: Module1.30 (GPIO6)
/CM4/CM4_Module1A/GPIO7: Module1.37 (GPIO7)
/CM4/CM4_Module1A/GPIO8: Module1.39 (GPIO8)
/CM4/CM4_Module1A/GPIO9: Module1.40 (GPIO9)
/CM4/CM4_Module1A/GPIO10: Module1.44 (GPIO10)
/CM4/CM4_Module1A/GPIO11: Module1.38 (GPIO11)
/CM4/CM4_Module1A/GPIO12: Module1.31 (GPIO12)
/CM4/CM4_Module1A/GPIO13: Module1.28 (GPIO13)
/CM4/CM4_Module1A/GPIO16: Module1.29 (GPIO16)
/CM4/CM4_Module1A/GPIO17: Module1.50 (GPIO17)
/CM4/CM4_Module1A/GPIO18: Module1.49 (GPIO18)
/CM4/CM4_Module1A/GPIO19: Module1.26 (GPIO19)
/CM4/CM4_Module1A/GPIO20: Module1.27 (GPIO20)
/CM4/CM4_Module1A/GPIO21: Module1.25 (GPIO21)
/CM4/CM4_Module1A/GPIO22: Module1.46 (GPIO22)
/CM4/CM4_Module1A/GPIO23: Module1.47 (GPIO23)
/CM4/CM4_Module1A/GPIO24: Module1.45 (GPIO24)
/CM4/CM4_Module1A/GPIO25: Module1.41 (GPIO25)
/CM4/CM4_Module1A/GPIO26: Module1.24 (GPIO26)
/CM4/CM4_Module1A/GPIO27: Module1.48 (GPIO27)
/CM4/CM4_Out_3.3V: Module1.84 (+3.3v_(Output)), Module1.86 (+3.3v_(Output)); also elsewhere on the board
/CM4/GLOBAL_EN_CM4: Q2.1; also elsewhere on the board
/CM4/GPIO_VREF_3.3V: Module1.78 (GPIO_VREF(1.8v/3.3v_Input)); also elsewhere on the board
/CM4/RUN_PG: Module1.92 (RUN_PG); also elsewhere on the board
/CM4/TRD0.D+: Module1.12 (Ethernet_Pair0_P); also elsewhere on the board
/CM4/TRD0.D-: Module1.10 (Ethernet_Pair0_N); also elsewhere on the board
/CM4/TRD1.D+: Module1.4 (Ethernet_Pair1_P); also elsewhere on the board
/CM4/TRD1.D-: Module1.6 (Ethernet_Pair1_N); also elsewhere on the board
/CM4/TRD2.D+: Module1.11 (Ethernet_Pair2_P); also elsewhere on the board
/CM4/TRD2.D-: Module1.9 (Ethernet_Pair2_N); also elsewhere on the board
/CM4/TRD3.D+: Module1.3 (Ethernet_Pair3_P); also elsewhere on the board
/CM4/TRD3.D-: Module1.5 (Ethernet_Pair3_N); also elsewhere on the board
/STM/PinoutSTM/USART2_RX: Module1.55 (GPIO14); also elsewhere on the board
/STM/PinoutSTM/USART2_TX: Module1.51 (GPIO15); also elsewhere on the board
GND: C1.2, C2.2, C3.2, C4.2, C5.2, C6.2, C7.2, C42.2, C47.2, Module1.1 (GND), Module1.2 (GND), Module1.7 (GND), Module1.8 (GND), Module1.13 (GND), Module1.14 (GND), Module1.22 (GND), Module1.23 (GND), Module1.32 (GND), Module1.33 (GND), Module1.42 (GND), Module1.43 (GND), Module1.52 (GND), Module1.53 (GND), Module1.59 (GND), Module1.60 (GND), Module1.65 (GND), Module1.66 (GND), Module1.71 (GND), Module1.74 (GND), Module1.89 (WL_nDisable), Module1.91 (BT_nDisable), Module1.98 (GND), Q2.2; also elsewhere on the board

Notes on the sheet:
N/A
connect Wlan to gnd if off, and leave floating for on. Please use a 2 pin connector here with a jumper cap. (has to be done)
GLOBAL_EN needs to be pulled low for >1ms after software shutdown.
Disable Wlan and Bluetooth?
Ethernet connection
GLOBAL_EN logic
Decoupling for CM4 5V inputs

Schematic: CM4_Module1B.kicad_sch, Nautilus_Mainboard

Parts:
C20: 4.7nF; C_0603_1608Metric; Voltage 50V; Tolerance 10%; MPN 885012206087; LCSC CXXXXX
D5: 595-TPD2EUSB30DRTR; TI_Prot_TPD2EUSB30DRTR; Mouser Part Number 595-TPD2EUSB30DRTR
D6: SMF5.0A-TP; SMF50ATP; MPN 833-SMF5.0A-TP
J3: 179-UJ20CHC4SMTTR; CON_Samesky_CUI_UJ20-C-H-C-4-SMT-TR; PARTREV 1.0
LED3: 710-150060RS83000; Wuerth_LED_150060RS83000; Manufacturer_Part_Number 150060RS83000
Module1: DF40C-100DS-0.4V(51); Con-Raspberry-Pi-4-Compute-Module; Part Description 100 Position Connector Receptacle, Cent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; LCSC N/A
R9: 1k; R_0603_1608Metric; Tolerance 1 %; MPN 560112116014; LCSC CXXXXX
R10, R12: 4.99k; R_0603_1608Metric; Tolerance 1 %; MPN 560112116132; LCSC CXXXXX
R11: 1M; R_0603_1608Metric; Tolerance 1 %; MPN 560112116074; LCSC CXXXXX

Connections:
/CM4/CM4_Module1B/PCIE_CLK._N: Module1.112 (PCIe_CLK_N); also elsewhere on the board
/CM4/CM4_Module1B/PCIE_CLK._P: Module1.110 (PCIe_CLK_P); also elsewhere on the board
/CM4/CM4_Module1B/PCIE_RX._N: Module1.118 (PCIe_RX_N); also elsewhere on the board
/CM4/CM4_Module1B/PCIE_RX._P: Module1.116 (PCIe_RX_P); also elsewhere on the board
/CM4/CM4_Module1B/PCIE_TX._N: Module1.124 (PCIe_TX_N); also elsewhere on the board
/CM4/CM4_Module1B/PCIE_TX._P: Module1.122 (PCIe_TX_P); also elsewhere on the board
/CM4/CM4_Module1B/PCIE_nRST: Module1.109 (PCIe_nRST); also elsewhere on the board
/CM4/CM4_Module1B/USB_D+: D5.2 (D-), J3.A6 (DP1), J3.B6 (DP2), Module1.105 (USB2_P)
/CM4/CM4_Module1B/USB_D-: D5.1 (D+), J3.A7 (DN1), J3.B7 (DN2), Module1.103 (USB2_N)
/CM4/CM4_Module1B/USB_OTG_ID: Module1.101 (USB_OTG_ID); also elsewhere on the board
/CM4/USB_Out_5V: D6.1 (K), J3.A4_B9 (VBUS), J3.A9_B4 (VBUS), LED3.2 (A); also elsewhere on the board
GND: C20.1, D5.3 (GND), D6.2 (A), J3.A1_B12 (GND), J3.A12_B1 (GND), Module1.107 (GND), Module1.108 (GND), Module1.113 (GND), Module1.114 (GND), Module1.119 (GND), Module1.120 (GND), Module1.125 (GND), Module1.126 (GND), Module1.131 (GND), Module1.132 (GND), Module1.137 (GND), Module1.138 (GND), Module1.144 (GND), Module1.150 (GND), Module1.155 (GND), Module1.156 (GND), Module1.161 (GND), Module1.162 (GND), Module1.167 (GND), Module1.168 (GND), Module1.173 (GND), Module1.174 (GND), Module1.179 (GND), Module1.180 (GND), Module1.185 (GND), Module1.186 (GND), Module1.191 (GND), Module1.192 (GND), Module1.197 (GND), Module1.198 (GND), R9.2, R10.2, R11.2, R12.2; also elsewhere on the board
unnamed: C20.2, J3.SH1 (SHIELD), J3.SH2 (SHIELD), J3.SH3 (SHIELD), J3.SH4 (SHIELD), R11.1
unnamed: J3.A5 (CC1), R10.1
unnamed: J3.B5 (CC2), R12.1
unnamed: LED3.1 (K), R9.1

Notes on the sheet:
old usb port for reference.
Can be kept floating. if no usb is connected
maybe RX and TX need to be switched
WIP, nRPI_BOOT? power only to certain parts? -> Diode (later) indication? (YES! LED)
Super important to not differ lengths or curve a lot with D+ and D-. Also should have same hole counts (vias) and same length.
ESD protection for the USB
USB Connection for CM4

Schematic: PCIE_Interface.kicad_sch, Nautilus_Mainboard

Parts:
J6: MDT275M02001; PCIE_MDT275M02001; Mouser Part Number 523-MDT275M02001
JP14, JP15, JP16, JP17: -; SolderJumper-2_P1.3mm_Open_RoundedPad1.0x1.5mm
LED4: 710-150060VS83000; Wuerth_LED_150060RS83000; Manufacturer_Part_Number 150060RS83000
R13: 1k; R_0603_1608Metric; Tolerance 1 %; MPN 560112116014; LCSC CXXXXX

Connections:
/CM4/Battery_Out_3.3V: J6.2, J6.4, J6.12, J6.14, J6.16, J6.18, J6.70, J6.72, J6.74, R13.2; also elsewhere on the board
/CM4/CM4_Module1B/PCIE_CLK._N: J6.53; also elsewhere on the board
/CM4/CM4_Module1B/PCIE_CLK._P: J6.55; also elsewhere on the board
/CM4/CM4_Module1B/PCIE_RX._N: J6.41; also elsewhere on the board
/CM4/CM4_Module1B/PCIE_RX._P: J6.43; also elsewhere on the board
/CM4/CM4_Module1B/PCIE_TX._N: J6.47; also elsewhere on the board
/CM4/CM4_Module1B/PCIE_TX._P: J6.49; also elsewhere on the board
/CM4/CM4_Module1B/PCIE_nRST: J6.50; also elsewhere on the board
/CM4/PCIE_Interface/CLKREQ#: J6.52
/CM4/PCIE_Interface/CONFIG_0: J6.21, JP14.2 (B)
/CM4/PCIE_Interface/CONFIG_1: J6.69, JP15.2 (B)
/CM4/PCIE_Interface/CONFIG_2: J6.75, JP16.2 (B)
/CM4/PCIE_Interface/CONFIG_3: J6.1, JP17.2 (B)
/CM4/PCIE_Interface/LED1_M2: J6.10, LED4.2 (A), R13.1
/CM4/PCIE_Interface/NFG1: J6.56
/CM4/PCIE_Interface/NFG2: J6.58
/CM4/PCIE_Interface/PERn1: J6.29
/CM4/PCIE_Interface/PERn2: J6.17
/CM4/PCIE_Interface/PERn3: J6.5
/CM4/PCIE_Interface/PERp1: J6.31
/CM4/PCIE_Interface/PERp2: J6.19
/CM4/PCIE_Interface/PERp3: J6.7
/CM4/PCIE_Interface/PETn1: J6.35
/CM4/PCIE_Interface/PETn2: J6.23
/CM4/PCIE_Interface/PETn3: J6.11
/CM4/PCIE_Interface/PETp1: J6.37
/CM4/PCIE_Interface/PETp2: J6.25
/CM4/PCIE_Interface/PETp3: J6.13
/CM4/PCIE_Interface/PEWAKE#: J6.54
/CM4/PCIE_Interface/SUSCLK: J6.68
GND: J6.3, J6.9, J6.15, J6.27, J6.33, J6.39, J6.45, J6.51, J6.57, J6.71, J6.73, J6.76 (MP_1), J6.77 (MP_2), JP14.1 (A), JP15.1 (A), JP16.1 (A), JP17.1 (A), LED4.1 (K); also elsewhere on the board

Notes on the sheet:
Led indicator
Configuration 0-Ohm resistors

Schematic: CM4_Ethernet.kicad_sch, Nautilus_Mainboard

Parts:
LED5: 710-150060VS83000; Wuerth_LED_150060RS83000; Manufacturer_Part_Number 150060RS83000
LED6: 710-150060YS83000; Wuerth_LED_150060RS83000; Manufacturer_Part_Number 150060RS83000
R7, R8: 1k; R_0603_1608Metric; Tolerance 1 %; MPN 560112116014; LCSC CXXXXX
TPD4EUSB30DQAR1, TPD4EUSB30DQAR2: IC_TPD4EUSB30DQAR; PARTREV F; LCSC C90627

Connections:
/CM4/Battery_Out_3.3V: LED5.2 (A), LED6.2 (A); also elsewhere on the board
/CM4/CM4_Module1A/ETH_LED_G: R7.1; also elsewhere on the board
/CM4/CM4_Module1A/ETH_LED_Y: R8.1; also elsewhere on the board
/CM4/TRD0.D+: TPD4EUSB30DQAR2.1, TPD4EUSB30DQAR2.10 (Through_1); also elsewhere on the board
/CM4/TRD0.D-: TPD4EUSB30DQAR2.2, TPD4EUSB30DQAR2.9 (Through_2); also elsewhere on the board
/CM4/TRD1.D+: TPD4EUSB30DQAR2.5, TPD4EUSB30DQAR2.6 (Through_5); also elsewhere on the board
/CM4/TRD1.D-: TPD4EUSB30DQAR2.4, TPD4EUSB30DQAR2.7 (Through_4); also elsewhere on the board
/CM4/TRD2.D+: TPD4EUSB30DQAR1.1, TPD4EUSB30DQAR1.10 (Through_1); also elsewhere on the board
/CM4/TRD2.D-: TPD4EUSB30DQAR1.2, TPD4EUSB30DQAR1.9 (Through_2); also elsewhere on the board
/CM4/TRD3.D+: TPD4EUSB30DQAR1.5, TPD4EUSB30DQAR1.6 (Through_5); also elsewhere on the board
/CM4/TRD3.D-: TPD4EUSB30DQAR1.4, TPD4EUSB30DQAR1.7 (Through_4); also elsewhere on the board
GND: TPD4EUSB30DQAR1.3, TPD4EUSB30DQAR1.8, TPD4EUSB30DQAR2.3, TPD4EUSB30DQAR2.8; also elsewhere on the board
unnamed: LED5.1 (K), R7.2
unnamed: LED6.1 (K), R8.2

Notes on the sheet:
POE Protection

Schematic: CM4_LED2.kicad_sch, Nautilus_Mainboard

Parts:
LED7: 710-150060YS83000; Wuerth_LED_150060RS83000; Manufacturer_Part_Number 150060RS83000
R6: 1k; R_0603_1608Metric; Tolerance 1 %; MPN 560112116014; LCSC CXXXXX

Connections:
/CM4/Battery_Out_3.3V: LED7.2 (A); also elsewhere on the board
/CM4/CM4_Module1A/CM4_LED2/PI_nLED_Activity: R6.1; also elsewhere on the board
unnamed: LED7.1 (K), R6.2

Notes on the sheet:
Simple Activity LED
Activity LED

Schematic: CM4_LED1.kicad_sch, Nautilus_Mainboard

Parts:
LED8: 710-150060YS83000; Wuerth_LED_150060RS83000; Manufacturer_Part_Number 150060RS83000
R5: 1k; R_0603_1608Metric; Tolerance 1 %; MPN 560112116014; LCSC CXXXXX
U3: Buffers & Line Driver; SOT65P210X110-5N; MPN 74LVC1G07SE-7; LCSC C67531

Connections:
/CM4/Battery_Out_3.3V: LED8.2 (A), U3.5 (VCC); also elsewhere on the board
/CM4/CM4_Module1A/CM4_LED1/nPWR_LED: U3.2; also elsewhere on the board
GND: U3.3 (GND); also elsewhere on the board
unnamed: LED8.1 (K), R5.2
unnamed: R5.1, U3.4

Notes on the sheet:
From the CM4 io board
Directly copied from the official CM4 io board (indicator LED for 3.3v)
Screenshot

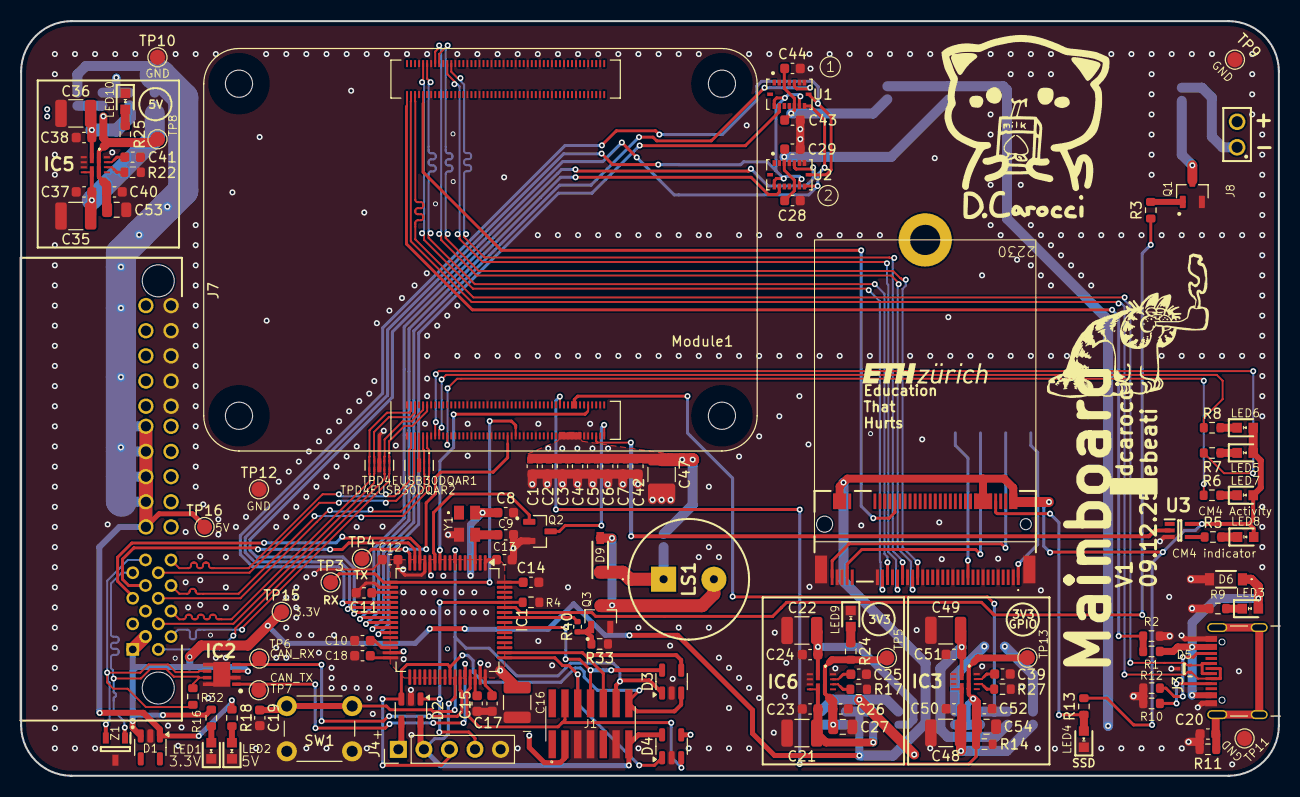
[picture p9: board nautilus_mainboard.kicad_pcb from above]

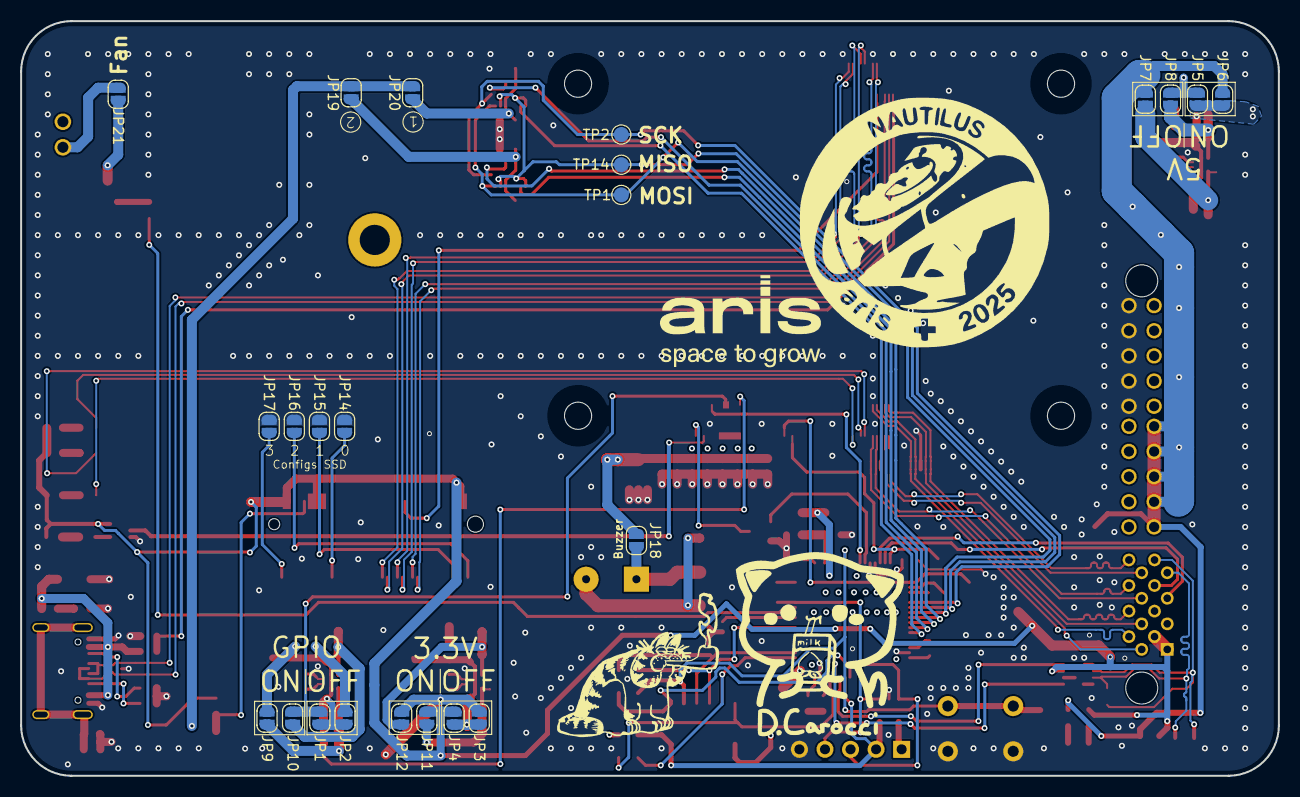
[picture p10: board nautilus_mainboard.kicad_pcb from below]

Board: 4 copper layers, 125.0 x 75.0 mm, 148 parts (23 on the bottom side), 100 nets.

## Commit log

2025-09-23 New Parts folder created, Additional pages for RTC created
    [PCF85063AT_AY.stp, RTC.kicad_sch, nautilus_mainboard.kicad_sch]
2025-10-14 Added Indicator LED to CM4
    [CM4_LED1.kicad_sch, CM4_Module1A.kicad_sch, CM4_Module1B.kicad_sch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]
2025-10-14 added gitignore, and did work on CM4
    [CM4_Ethernet.kicad_sch, CM4_LED1.kicad_sch, CM4_LED2.kicad_sch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]
2025-10-15 started with the new STM integration
    [PinoutSTM.kicad_sch]
2025-10-16 Added other LED indicators, ethernet and connector (main connector to other pcb's)
    [CM4_Ethernet.kicad_sch, CM4_LED1.kicad_sch, CM4_LED2.kicad_sch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]
2025-10-17 minor changes/cleanup
    [CM4.kicad_sch, CM4_Ethernet.kicad_sch, CM4_LED1.kicad_sch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]
2025-10-17 readded RX and TX, Corrected DZ_PATHS to be relative instead of absolute.
    [CM4_Module1A.kicad_sch]
2025-10-17 Added usb connector
    [CM4_Module1B.kicad_sch, LPHT-connector.kicad_sch, nautilus_mainboard.kicad_sch]
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2025-10-18 Comments (+ new Connector?)
    [CM4_Module1A.kicad_sch, CM4_Module1B.kicad_sch, LPHT-connector.kicad_sch]
2025-10-21 Changed template of the sheet
    [CM4_Module1A.kicad_sch, CM4_Module1B.kicad_sch, nautilus_mainboard.kicad_sch]
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2025-10-21 WIFI connection changes PI
    [CM4.kicad_sch, CM4_Module1A.kicad_sch, CM4_Module1B.kicad_sch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]
2025-10-21 resolve project breaking merge conflict miss
    [PinoutSTM.kicad_sch]
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2025-10-21 Connected the Uart lines
    [STM.kicad_sch, nautilus_mainboard.kicad_sch]
2025-10-21 Implemented the entire can tranciever
    [PowerSTM.kicad_sch, STM.kicad_sch]
2025-10-22 added more support for the ssd and fixed LED configuration
    [CM4.kicad_sch, CM4_Ethernet.kicad_sch, CM4_LED2.kicad_sch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]
2025-10-26 multiple changes. fixed some mistakes, added jumper pins for wifi
    [CM4.kicad_sch, CM4_Module1A.kicad_sch, CM4_Module1B.kicad_sch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]
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2025-10-28 not working power distribution
    [Power_logic.kicad_sch, nautilus_mainboard.kicad_sch]
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2025-10-28 added connections for can
    [PowerSTM.kicad_sch, STM.kicad_sch]
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2025-10-28 Added Power logic finally. (plus some comments on further improvements)
    [3.3V_Logic.kicad_sch, 5V_Logic.kicad_sch, CM4.kicad_sch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]
2025-10-29 tried to find some placements for power routing
    [5V_Logic.kicad_sch, CM4_Module1A.kicad_sch, CM4_Module1B.kicad_sch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]
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2025-11-01 swapped vref and logic position
    [nautilus_mainboard.kicad_pcb]
2025-11-01 checked the whole schematic with the datasheet, took notes/questions in the datasheet (pdf also uploaded)
    [CM4.kicad_sch, CM4_Module1A.kicad_sch, CM4_Module1B.kicad_sch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]
2025-11-02 multiple changes to the differential pair for easier routing later.
    [CM4_Ethernet.kicad_sch, CM4_Module1B.kicad_sch, Power_logic.kicad_sch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]
2025-11-03 added Gyroscope and Accelerometer part (4x) over IIC
    [3.3V_Logic.kicad_sch, 5V_Logic.kicad_sch, CM4_Ethernet.kicad_sch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]
2025-11-03 4x accel and gyro, added pi stl
    [nautilus_mainboard.kicad_pcb]
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2025-11-04 new outline of board plus first traces
    [3.3V_Logic.kicad_sch, IMU.kicad_sch, IMU1.kicad_sch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]
2025-11-04 first tries with signal tracks
    [nautilus_mainboard.kicad_pcb, nautilus_mainboard.kicad_sch]
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2025-11-10 fixed the can tranciever placement
    [nautilus_mainboard.kicad_pcb]
2025-11-10 updated some diff pairs to be nicer
    [nautilus_mainboard.kicad_pcb]
2025-11-10 cleaned up some schematic problems
    [CM4_Module1A.kicad_sch, LPHT-connector.kicad_sch, PinoutSTM.kicad_sch]
2025-11-11 multiple chainges on PCB
    [3.3V_Logic.kicad_sch, 5V_Logic.kicad_sch, CM4.kicad_sch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]
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2025-11-15 multiple rearrangements of the PCB
    [nautilus_mainboard.kicad_pcb]
2025-11-15 feat: added multiple new routes to the PCB
    [CM4_LED2.kicad_sch, CM4_Module1A.kicad_sch, nautilus_mainboard.kicad_pcb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]
2025-11-15 feat: new decoupling for STM chore: rethink the decoupling strategy for STM module (imo wayy too small)
    [nautilus_mainboard.kicad_pcb]
2025-11-15 feat: nearly all connections done
    [nautilus_mainboard.kicad_pcb]
2025-11-15 nearly complete with the PCB
    [CM4_LED1.kicad_sch, IMU1.kicad_sch, IMU2.kicad_sch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]
2025-11-16 fix: widened the power tracks for 5V line
    [nautilus_mainboard.kicad_pcb]
2025-11-16 added piezzo circuit and i2c line
    [Piezzo.kicad_sch, PinoutSTM.kicad_sch, STM.kicad_sch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]
2025-11-16 fix: fixed multiple DRC warnings and errors. Had to adjust pad clearances from 0.2mm to 0.15mm to pass DTC. Should be addressed and checked with the manifacturer if those conditions are acceptable. f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
    [nautilus_mainboard.kicad_pcb]
2025-11-16 fix: adjusted copper to hole distance from 0.25mm to 0.2mm in order to meet the USB-C tolerances needed to use it.
    [nautilus_mainboard.kicad_pcb]
2025-11-16 tented the vias(gnd) and routed the i2c and fan control path
    [PinoutSTM.kicad_sch, nautilus_mainboard.kicad_pcb]
2025-11-16 chore: remove DRC for pads being too close, or find a solution
    [nautilus_mainboard.kicad_pcb]
2025-11-16 removed unused parts (piezzo) form pcb
    [nautilus_mainboard.kicad_pcb]
2025-11-16 fix: adjusted clearance in order to pass DRC checks for BMI088
    [nautilus_mainboard.kicad_pcb]
2025-11-16 chore: added a comment that piezzo buzzer wont be implemented right now
    [Piezzo.kicad_sch]
2025-11-16 chore: removed old hirarchical lables that were not being used anymore
    [CM4.kicad_sch]
2025-11-17 added the stmv3 connector and fixed the issues
    [PinoutSTM.kicad_sch, PowerSTM.kicad_sch, nautilus_mainboard.kicad_pcb]
2025-11-17 fixed pcb errors
    [nautilus_mainboard.kicad_pcb]
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2025-11-17 refilled all copper zones
    [CM4_Module1B.kicad_sch, nautilus_mainboard.kicad_pcb]
2025-11-18 added debugger pinout picture
    [PinoutSTM.kicad_sch]
2025-11-18 added can termination resistance and esd protection
    [PowerSTM.kicad_sch]
2025-11-18 changed the piezzo buzzer
    [Piezzo.kicad_sch, PinoutSTM.kicad_sch, PowerSTM.kicad_sch]
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2025-11-18 fix: 2 ERC errors fixed
    [3.3V_Logic.kicad_sch, CM4_Module1A.kicad_sch]
2025-11-18 chore: multiple cosmetic wiring changes
    [3.3V_Logic.kicad_sch, 5V_Logic.kicad_sch, CM4.kicad_sch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]
2025-11-18 chore: Many routing changes
    [3.3V_Logic.kicad_sch, CM4.kicad_sch, CM4_Ethernet.kicad_sch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]
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2025-11-19 chore: added LED indicators for power and activity status, updated symbold, rerouted some things for better visibility
    [3.3V_Logic.kicad_sch, 5V_Logic.kicad_sch, CM4.kicad_sch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]
2025-11-19 chore: Loads of redoing stuff. Added a Changelog
    [3.3V_Logic.kicad_sch, 5V_Logic.kicad_sch, CM4.kicad_sch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]
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2025-11-19 Part placing 60% done
    [nautilus_mainboard.kicad_pcb, nautilus_mainboard.kicad_sch]
2025-11-20 feat: added a lot of traces in PCB
    [LPHT-connector.kicad_sch, PinoutSTM.kicad_sch, nautilus_mainboard.kicad_pcb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]
2025-11-23 chore: new testpoint symbols
    [STM.kicad_sch, nautilus_mainboard.kicad_pcb, nautilus_mainboard.kicad_sch]
2025-11-24 chore: routed many parts together. added testpoints
    [CM4_Module1B.kicad_sch, GPIO_REF3.3V.kicad_sch, PowerSTM.kicad_sch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]
2025-11-25 chore: routed some parts, updated footprints, fixed unaligned footprints.
    [nautilus_mainboard.kicad_pcb]
2025-11-25 replaced the TSV diode for can with a new one
    [PowerSTM.kicad_sch]
2025-11-25 Changed the crystal to a active oscillator
    [PinoutSTM.kicad_sch]
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2025-11-25 forgrot to add a 15pf cap and a 100n cap to the oscillator
    [PinoutSTM.kicad_sch]
2025-11-25 fix: replaced 0402 components with 0603
    [PinoutSTM.kicad_sch]
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2025-11-25 chore: replaced 0 ohm with jumpers (not complete)
    [PCIE_Interface.kicad_sch, Piezzo.kicad_sch, PinoutSTM.kicad_sch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]
2025-11-26 chore: routed the Jumpers (incomplete) fix: removed all leftover 0Ohm resistors
    [IMU1.kicad_sch, IMU2.kicad_sch, PCIE_Interface.kicad_sch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]
2025-11-28 chore: more routing + pin adjustments
    [PinoutSTM.kicad_sch, nautilus_mainboard.kicad_pcb]
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2025-12-01 fix: removed unused pin for outside fan voltage supply
    [PinoutSTM.kicad_sch, nautilus_mainboard.kicad_pcb]
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2025-12-02 chore: added fun rotation to the cat, revoved eth logo
    [nautilus_mainboard.kicad_sch]
2025-12-09 fix: minor changes, preparations for BOM and gerber, added Stitching
    [3.3V_Logic.kicad_sch, 5V_Logic.kicad_sch, CM4.kicad_sch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]
